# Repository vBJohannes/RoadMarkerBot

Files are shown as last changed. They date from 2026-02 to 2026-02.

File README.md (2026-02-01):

# DISCLAIMER: THIS REPOSITORY IS STILL IN DEVELOPMENT AND NOT ALL PARTS ARE DOCUMENTED YET.

# RoadMarkerBot

A road marking rover with

- skid steering,
- differential GPS (Base + Rover),
- ArduPilot,
- multiple colors,
- dual use as a survey tool.

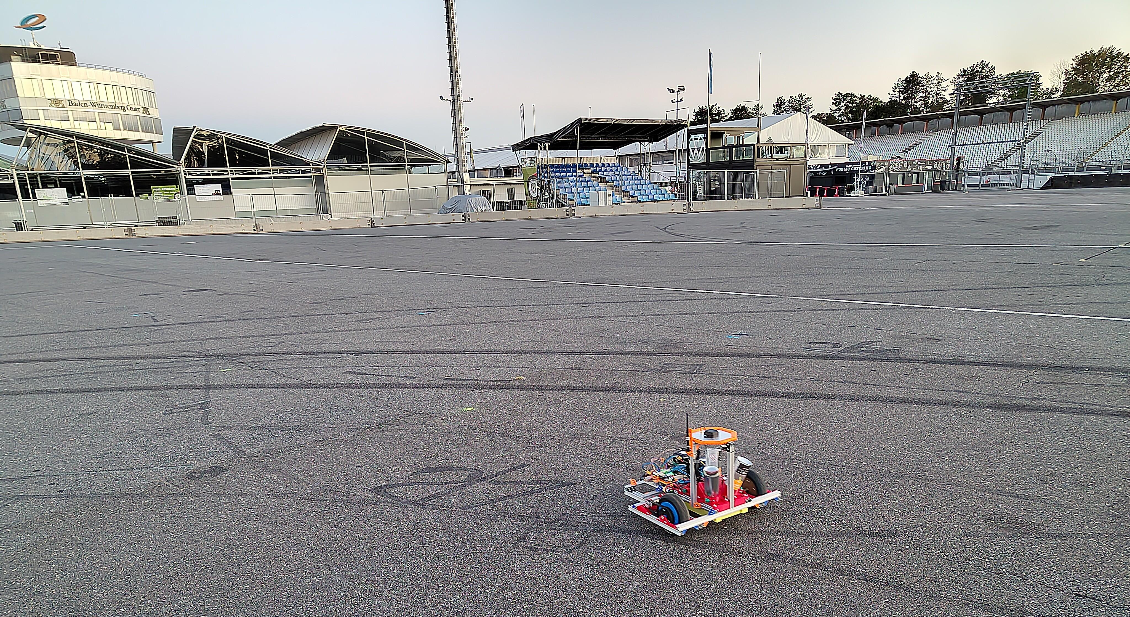
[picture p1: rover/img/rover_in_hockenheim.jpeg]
Bot_during_work


## License

Everything described here can be freely worked in compliance with CC BY-NC-SA 4.0. Please see [License](./LICENSE) for further clarification or check [here](https://creativecommons.org/licenses/by-nc-sa/4.0/deed.en).

## Requirements

- The rover should be able to spray a dot onto pavement at a position defined by GPS.
- The rover should be remotely controllable in order to halt its operation, move around obstacles, and manually drive it for small distances.
- The rover should accept a series of GPS positions in order to mark more complicated tracks.
- The rover should ideally be constructed from off-the-shelf components for easy replacement.
- Rover GPS can be also used as survey tool for manual measurements without the need to move the rover there.

## Solution

The system is divided into subsystems in order to fulfil the requirements.

- The rover is constructed a skid steer robot to realize turning on the spot.
- The rover uses differential GPS for accurate positioning.
- The rover uses ArduPilot in order to provide a platform for vehicle movement and an interface to input target GPS positions.
- The rover can carry four different spray cans at once to use different colors without manual interaction.
- The rover is controlled with an ELRS rc controller in order to provide easy manual input.
- The rover is mainly constucted from aluminium extrusions, 3D prints, rc hobby electronics and available software.

### Architecture

```mermaid
graph TD
    %% Rover
    subgraph ROVER [Rover]
        AP_ROVER(ArduPilot)
        TELEM_ROVER(Rover Communication Module)
        GPS_ROVER(GPS Module)
        GPS_CORR_ROVER(GPS Communication Module)
    end

    subgraph sg1 [GPS Base Station]
        GPS_BASE(GPS Module)
        GPS_CORR_BASE(GPS Communication Module)
    end

    subgraph MP_BASE [Rover Control Base Station]
        AP_BASE(ArduPilot Mission Planner)
        TELEM_BASE(ArduPilot Base Station Communication Module)
    end

    %% Connections
    TELEM_ROVER <-. "Telemetry Data" .-> TELEM_BASE
    GPS_CORR_BASE -. "GPS Correction Data" .-> GPS_CORR_ROVER
    GPS_CORR_ROVER --> GPS_ROVER
    GPS_ROVER --> AP_ROVER
    TELEM_ROVER <--> AP_ROVER
    TELEM_BASE <--> AP_BASE
    GPS_BASE --> GPS_CORR_BASE
```

### In Detail

[Rover Documentation](./rover/README.md)<br>
[GPS Base Station Documentation](./rover/config.md)<br>
[Control Base Station Documentation](./rover/config.md)<br>
[Survey Tool Documentation](./rover/config.md)

## Known Issues

- ArduPilot on Rover currently can only handle around 100 waypoints.
- Rover initialization is currently driving in a large circle to be able to fully use the gyroscope. Magnetometer is currently disabled due to inreliable operation. Hence initial heading is unclear to ArduPilot and it needs to calibrate itself using gyroscope in GPS before starting any mission.
- Starting any movement looks a little jenky and stopping is quite abrupt, which hints to improper PID calibration or ESC configuration.

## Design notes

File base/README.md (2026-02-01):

# GPS Base Station

## Architecture

```mermaid
graph TD
    %% Power Source
    PB(USB Power Bank or<br>other power source) -- "5V via USB" --> BASE_GPS(RTK GPS Module)

    %% Internal Connection
    BASE_GPS -- "UART (RTCM3x)" --> RADIO(Radio Module<br>of Base Station)
    ANT(GPS Antenna) -- "Signal" --> BASE_GPS

    %% Wireless Output
    RADIO -. "868 MHz RTCM Corrections" .-> ROVER(Radio Module<br>on Rover)
```

## Design

The GPS base station is a rather simple setup and was put together from remaining parts and simple 3D printed parts in order to make a solid yet reliable device.
It is about 1000mm in height (to get the antenna off the ground without being too susceptable to wind) and the metal shield at the top has an excessive 300mm diameter (to reduce reflections as much as possible).
It is also built from 20x20mm aluminium extrusions.
The whole system is powered by a regular powerbank and will run for quite some time on it as is only draws about 150mA of current when sending correction data.
The antenna is put to the corner of the upper shield to be also elevated off the ground.

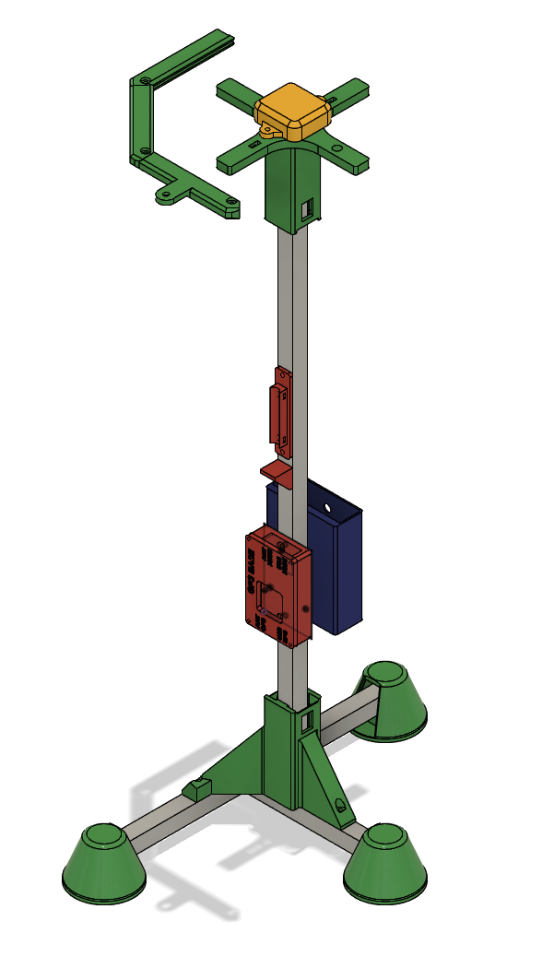
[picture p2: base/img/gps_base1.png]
gps_base1

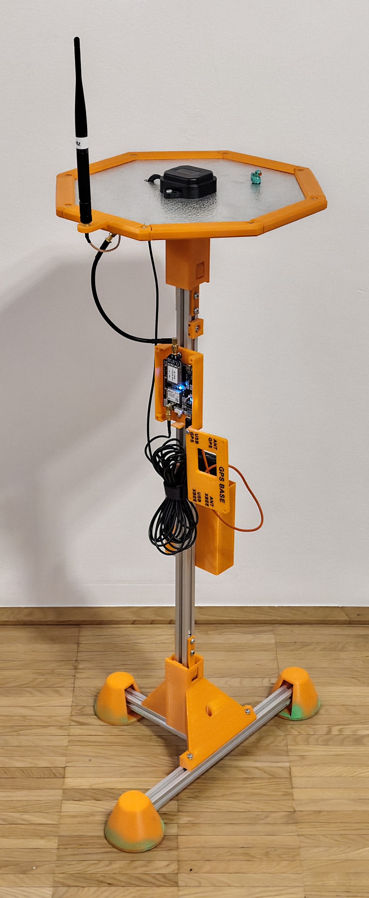
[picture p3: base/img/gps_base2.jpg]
gps_base2

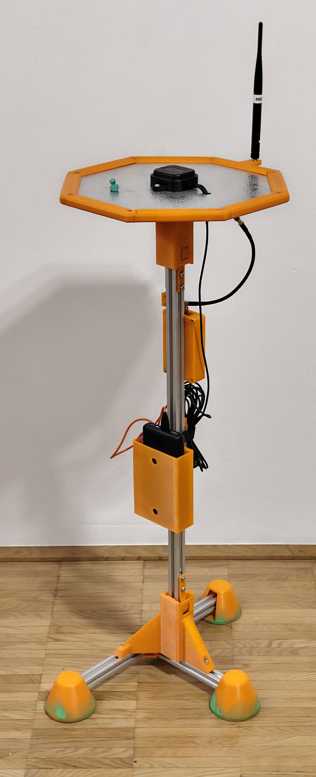
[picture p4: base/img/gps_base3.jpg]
gps_base3

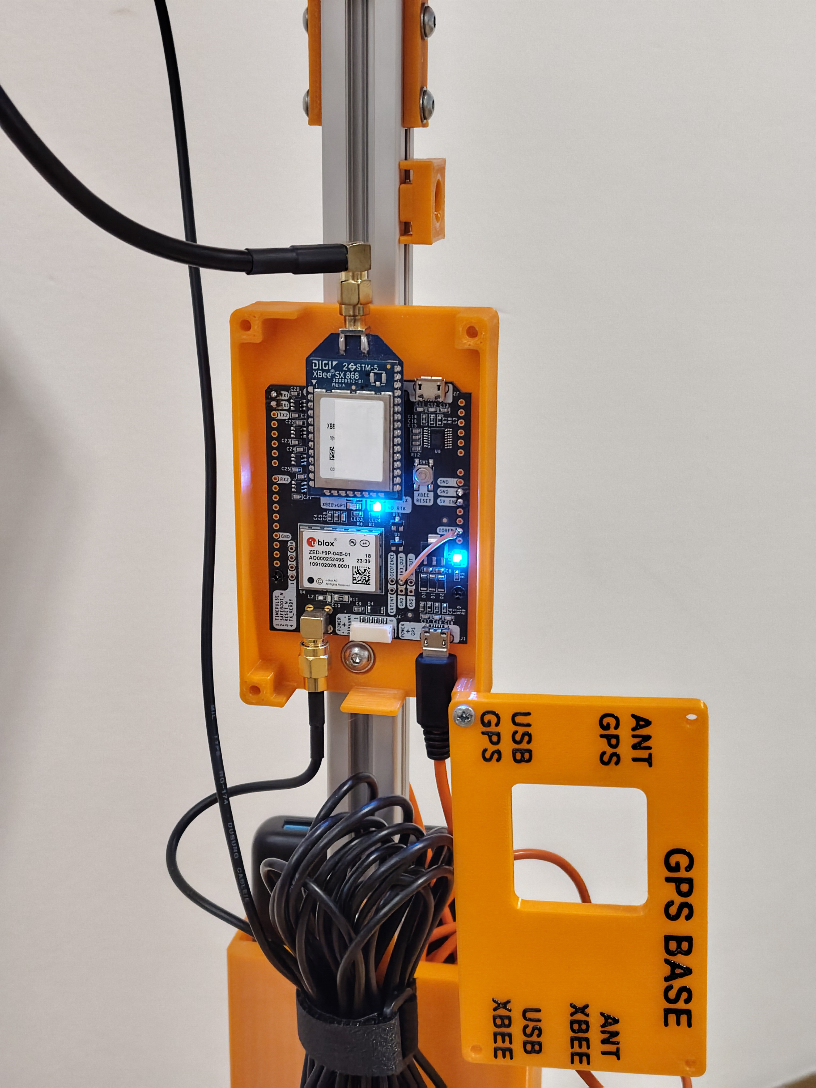
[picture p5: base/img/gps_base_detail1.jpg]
gps_base_detail1

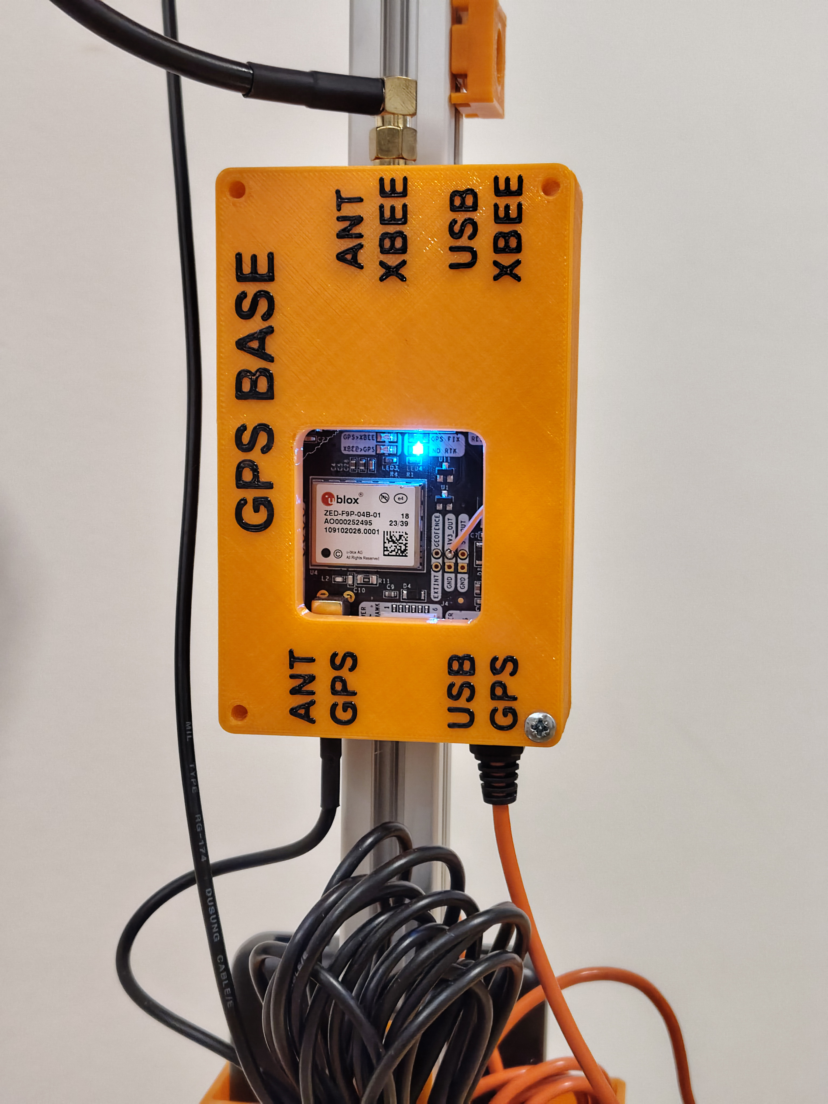
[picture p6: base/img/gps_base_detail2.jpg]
gps_base_detail2


## Usage

- The antenna is placed on a dedicated spot and the ground is marked so the antenna can be placed there repeatedly in the exact same position.
- Ideally the spot is surveyed in by using the antenna, a laptop with [u-Center](https://www.u-blox.com/en/product/u-center), some free Ntrip data service like [RTK2Go](http://rtk2go.com), and the rover GPS config (see [Rover GPS Config](ROVER_LINKS)) to find the exact position the GPS is currently in.
This can then be entered in the config of the GPS base station to run it in fixed mode.
- Both communication modules need to use the same config to communicate properly.

## Links

[GPS Base uBlox Config](./config/uBlox_F9P_Base_config.txt)<br>
[XBee RTCM Config](./config/GPS_RTCM_XBeeSX686_fwA00A.xpro)<br>
[CAD files](./cad/)

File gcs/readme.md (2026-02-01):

# Overview

The Ground Control Station is needed to send the mission waypoints to the rover and communicate with it in the field.
For that it is easiest to run a software like [Mission Planner](https://ardupilot.org/planner/docs/mission-planner-installation.html) and have a reliable connection to the rover.
This can be a USB cable, WiFi, an pair of 868MHz radio modules, or another sort of communication.
In this project a XBee SX 686 module was used, which had the advantage of substantial range at the expense of insanely slow bulk data transfer.
The profile of the modules can be found [HERE](./config/HostTelemetry_XBeeSX686_fwA00A.xpro) and can be used with the [XCTU Tool](https://www.digi.com/products/embedded-systems/digi-xbee/digi-xbee-tools/xctu) to configure the module.
**Hint:** The guard time in that profile is set to 5000ms and this needs to be configured in the XCTU Tool itself as well.

## Mission Planner

For this project v1.3.82 was used.
Choose the proper COM port to get access to the data coming from the XBee module.
In this project a 115200 8N1 was chosen as baud rate.
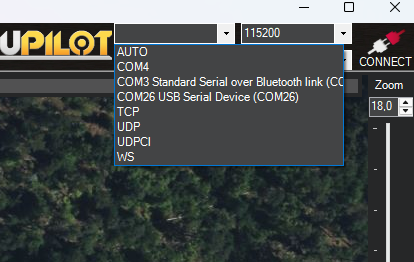
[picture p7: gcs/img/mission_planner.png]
mission_planner


## Equipment

### Case

In this project a nice little case was designed, that was intended to house two modules, but was used by only one in the end.
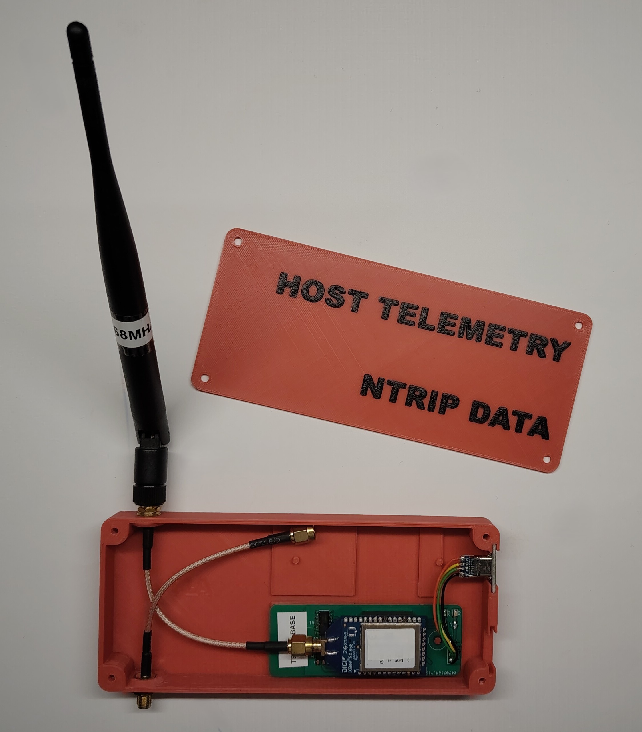
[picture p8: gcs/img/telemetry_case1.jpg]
telemetry_case1

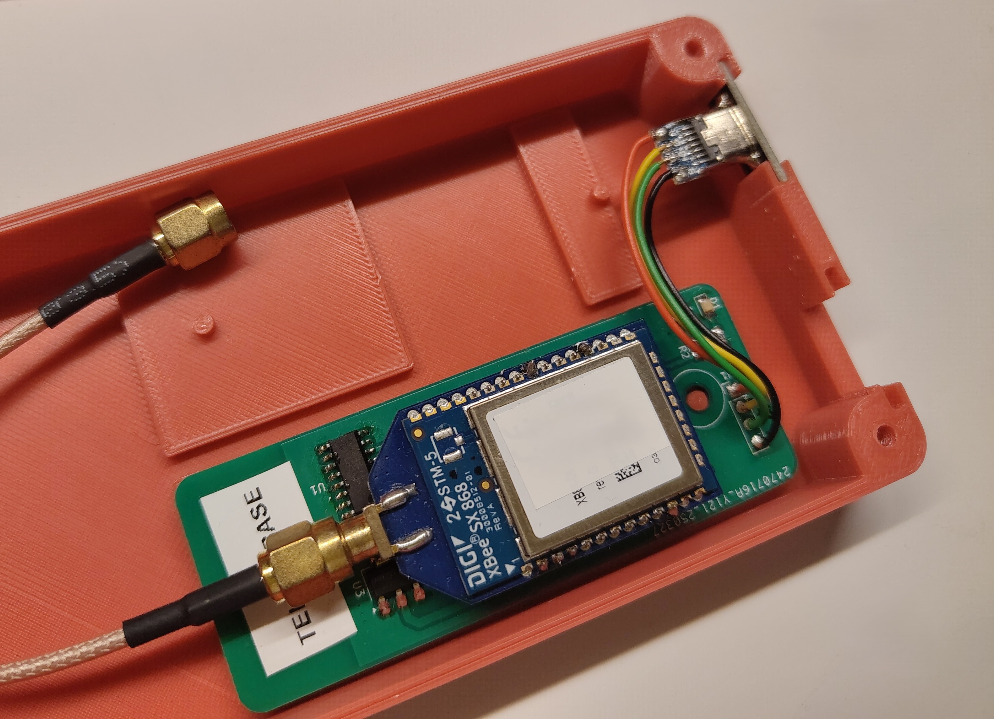
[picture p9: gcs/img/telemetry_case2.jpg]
telemetry_case2


### PCB

For this project a custom PCB was designed. The KiCAD project can be found [HERE](./cad/telemetry_pcb.zip).
The lower picture shows an earlier version of the board.
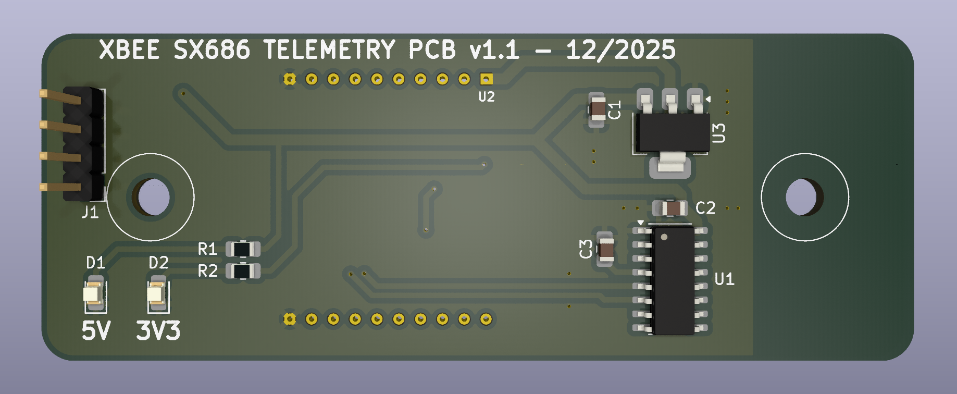
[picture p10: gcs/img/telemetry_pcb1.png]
telemetry_pcb1

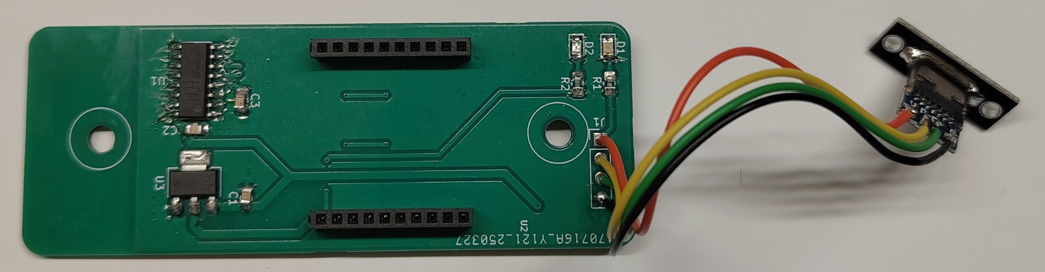
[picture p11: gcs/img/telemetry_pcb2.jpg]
telemetry_pcb2


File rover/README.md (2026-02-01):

# Rover

## Logical Architecture

```mermaid
graph TD
    %% Central Unit
    subgraph PIXHAWK [Pixhawk 2.4.8]
        AP(ArduPilot)
        CPU(Processor)
        IMU_INT(Internal Gyro / IMU)
    end

    %% Sensors & Inputs
    IMU_EXT(External Gyro) -- "I2C Bus" --> PIXHAWK
    GPS_ROVER(RTK GPS Rover) -- "UART" --> PIXHAWK
    RC_REC(RC Receiver) -- "UART" --> PIXHAWK
    TELE(Telemetry Module) -- "UART (MAVLink)" --> PIXHAWK
    
    %% Power Monitoring (New)
    PWR_SENS(Power Sensor) -- "Analog (U/I Data)" --> PIXHAWK

    %% Wireless Links
    GCS(Ground Control Station<br>Ardupilot Mission Planner) <-. "868 MHz Radio" .-> TELE
    Remote(Remote Control<br>with EdgeTX) <-. "ELRS Link" .-> RC_REC

    %% GPS RTK
    GPS_BASE(RTK GPS Base Station) -. "868 MHz RTCM Corrections" .-> GPS_ROVER

    %% Actuators (Outputs)
    PIXHAWK -- "PWM" --> ESC(ESC Motor Controller<br>AM32)
    ESC --> MOT(2x BLDC Drive Motors)
    
    PIXHAWK -- "PWM" --> SER(4x Servos<br>for Spray Cans)
```

## Electrical Archtecture

```mermaid
graph TD
    %% Power Source and Monitoring
    BAT(4-6S LiPo Battery) --> SENS(Power Sensor / <br/>Current & Voltage)
    
    %% Monitoring Link
    SENS -- "Analog Data (U/I)" --> PH(Pixhawk Flight Controller)

    %% Direct Power Distribution
    SENS --> ESC(Dual ESC<br/>Motor Controller)
    SENS --> REG1(5V Voltage Regulator<br/>Logic Supply)
    SENS --> REG2(5V Voltage Regulator<br/>Servo Supply)

    %% Drive System
    ESC --> M1(Drive Motor Left)
    ESC --> M2(Drive Motor Right)

    %% Logic Supply Path
    REG1 --> PH
    PH --> GPS(RTK GPS Rover)
    PH --> TELE(Telemetry Module)
    PH --> RC(RC Receiver)
    PH --> GYRO(External Gyro / IMU)

    %% Servo Supply Path
    REG2 --> SERVO_BUS(Servo Rail)
    SERVO_BUS --> S_ALL(4x Servos)

    %% Control Signals (Simplified)
    PH -. "PWM" .-> ESC
    PH -. "PWM" .-> S_ALL
```

## Design

The robot was designed as a skid steer vehicle with a trailing third wheel.
An extensible design was chosen to allow quick modifications.
Overall vehicle dimensions: width 600 mm, length 500 mm, height 400 mm

Built with:

- 20×20 mm aluminium extrusions to mount various components
- high gear reduction on the motors for precise maneuvers
- simple power supply using 18 V batteries compatible with Makita or Bosch
- readily available hobby-model parts
- autonomous control via ArduPilot software
- four spray cans can be mounted and all spray to the same point

### Frame

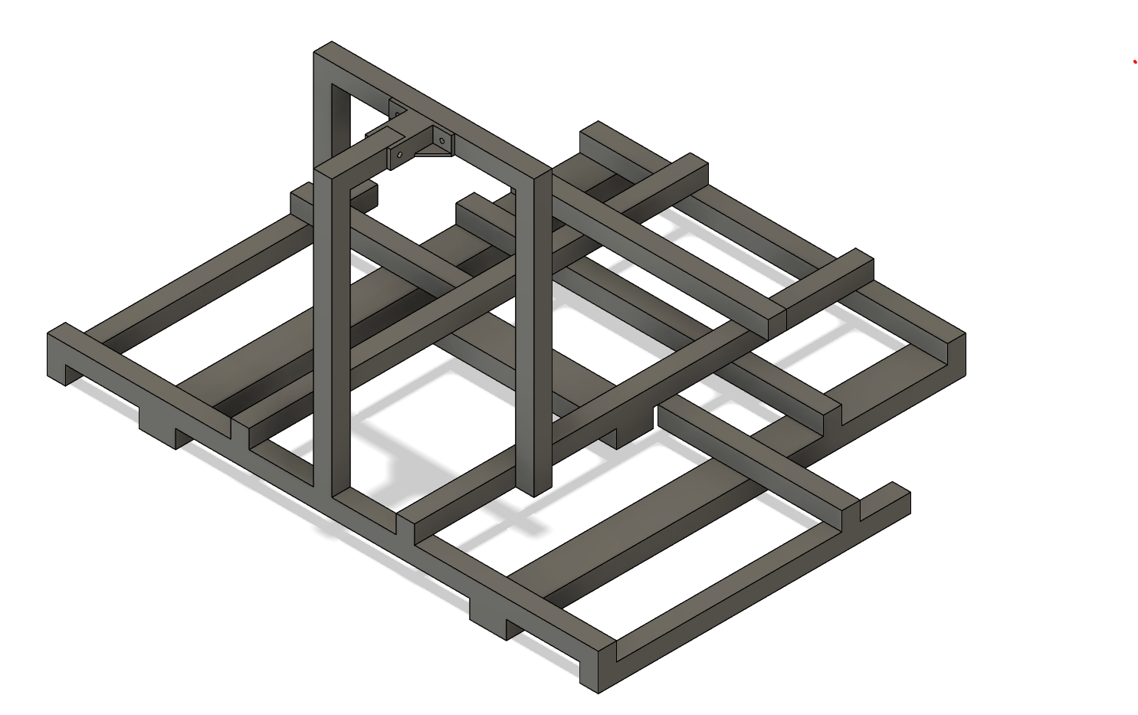
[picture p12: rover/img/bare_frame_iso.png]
frame_iso

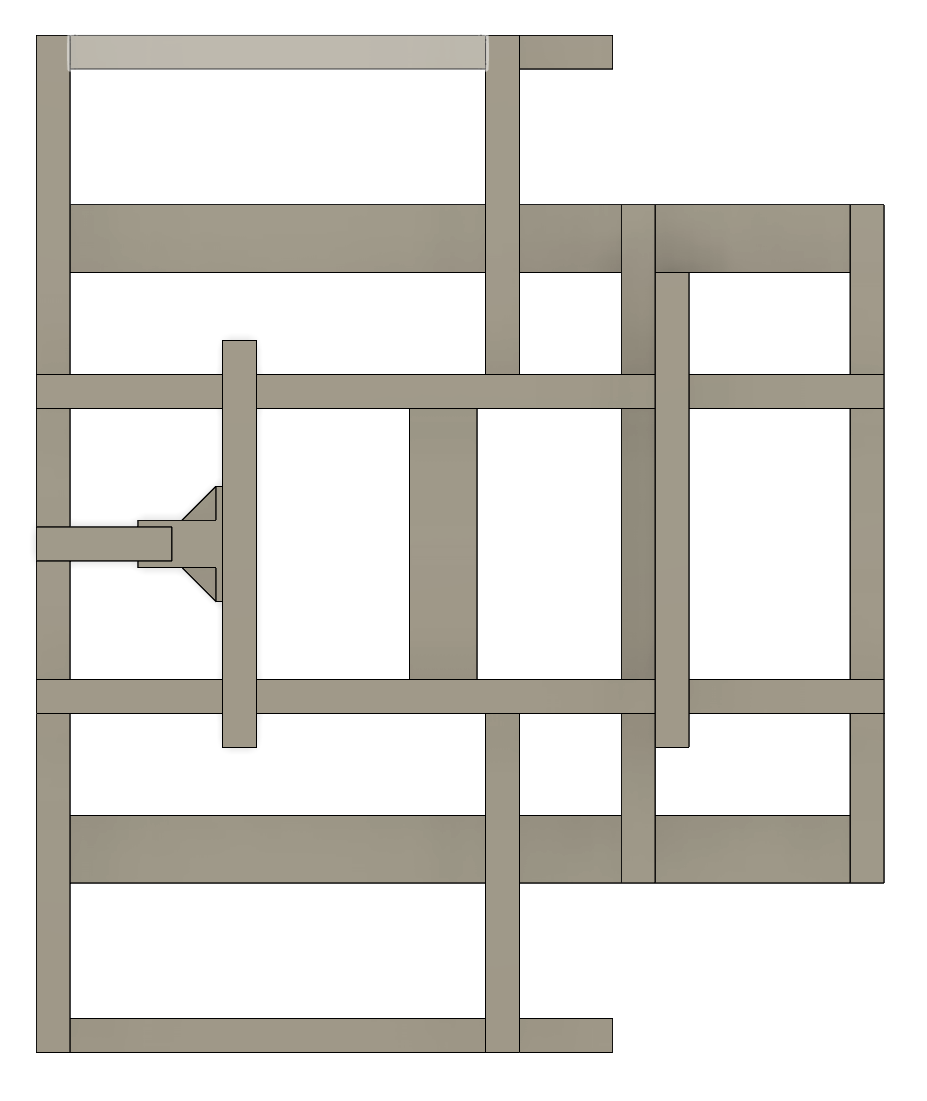
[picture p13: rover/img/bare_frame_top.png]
frame_top


### Wheel Assembly

For this project powerful and low-KV motors were used.
The purpose was to make small corrections with the high torque and low rpm.
In addition a reduction of about 45:1 was achieved by a gearbox (19:1) and pulleys (2.35:1).
This specific BLDC motor is a *Robbe 5052 410K/V* rated for 50A at 6S.
Due to the reduction the rover reaches speeds of about 5km/h.
The wheel itself is a solid rubber 190mm replacement wheel for e-scooters and was adapted to carry a pully.
The third wheel in the back was purchased in a local hardware store and the wheel itself was reprinted in TPU in order to run smoother on hard surfaces like concrete.
All the parts can be found in [this archive (MISSING)](./cad/motor_wheel_parts.zip).

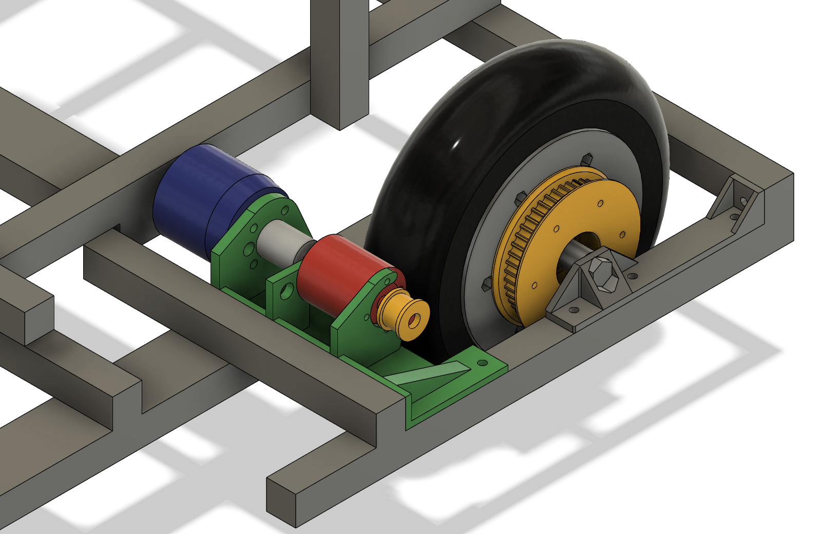
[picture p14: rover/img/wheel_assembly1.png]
wheel_assembly1

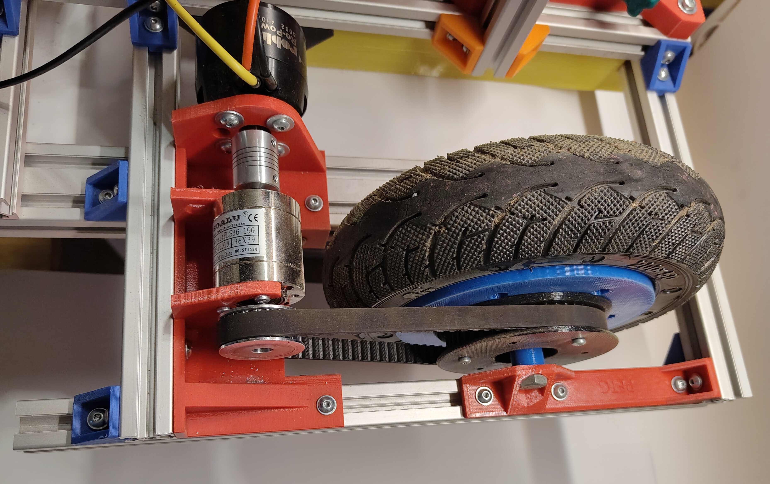
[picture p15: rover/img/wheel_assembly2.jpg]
wheel_assembly2

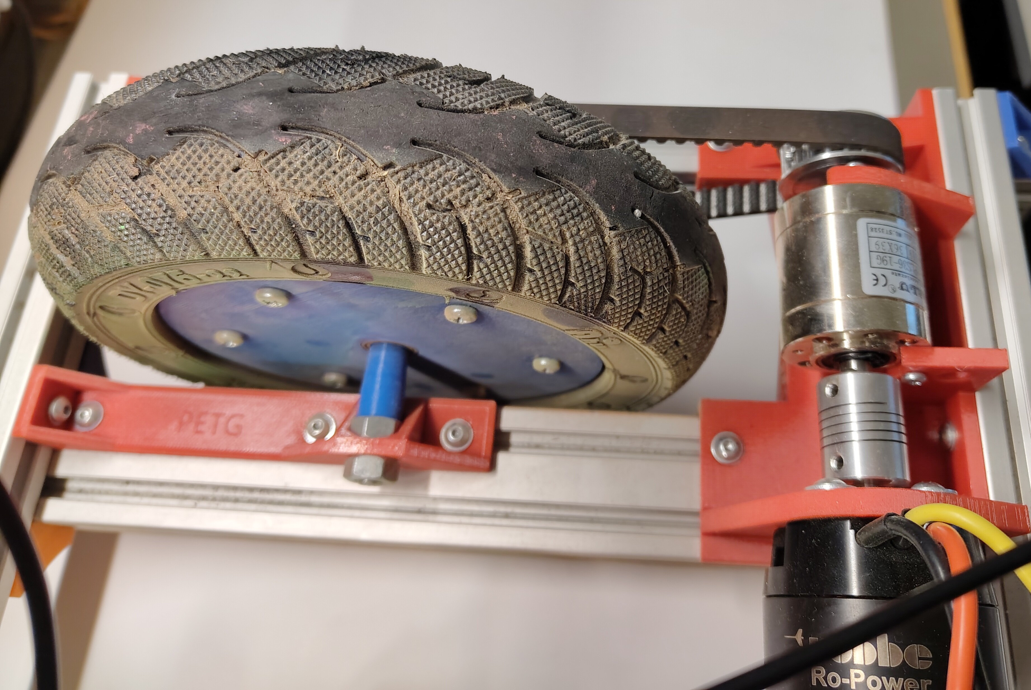
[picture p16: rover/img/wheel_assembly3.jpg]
wheel_assembly3

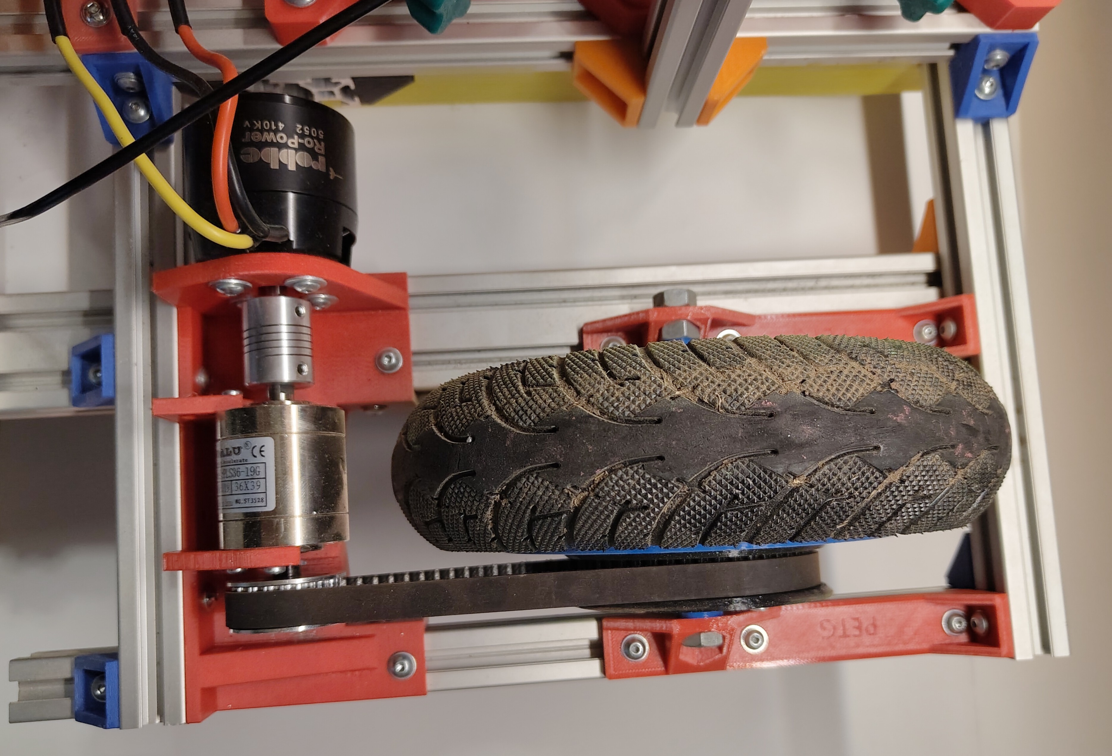
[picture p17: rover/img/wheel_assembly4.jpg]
wheel_assembly4

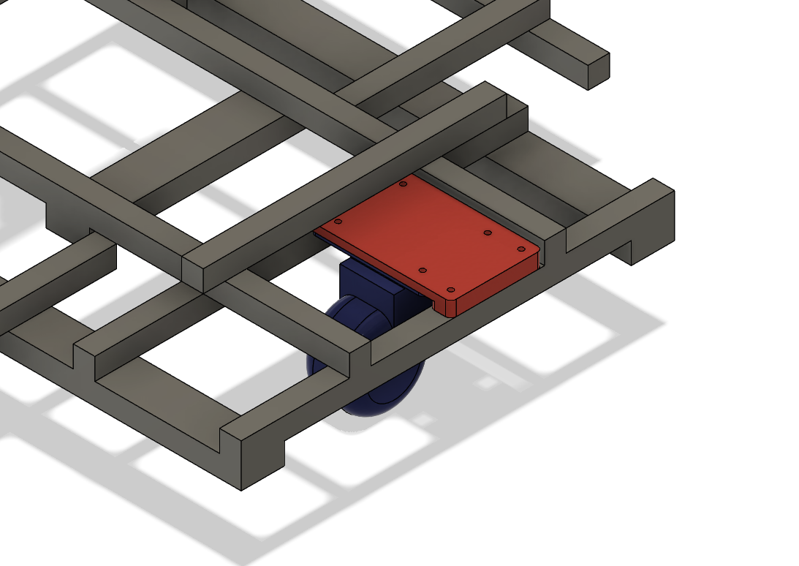
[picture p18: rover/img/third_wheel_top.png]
third_wheel_top

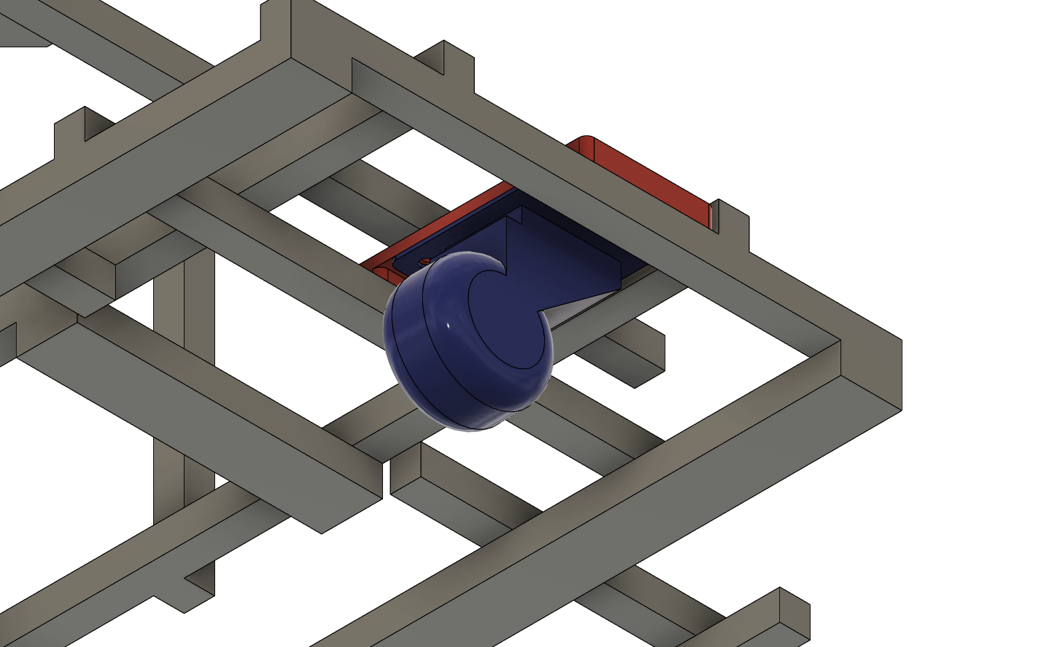
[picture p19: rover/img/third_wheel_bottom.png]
third_wheel_bottom

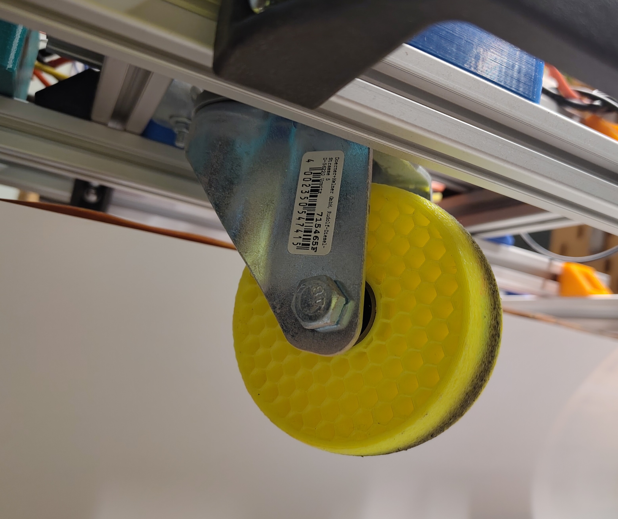
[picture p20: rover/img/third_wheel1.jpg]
third_wheel1

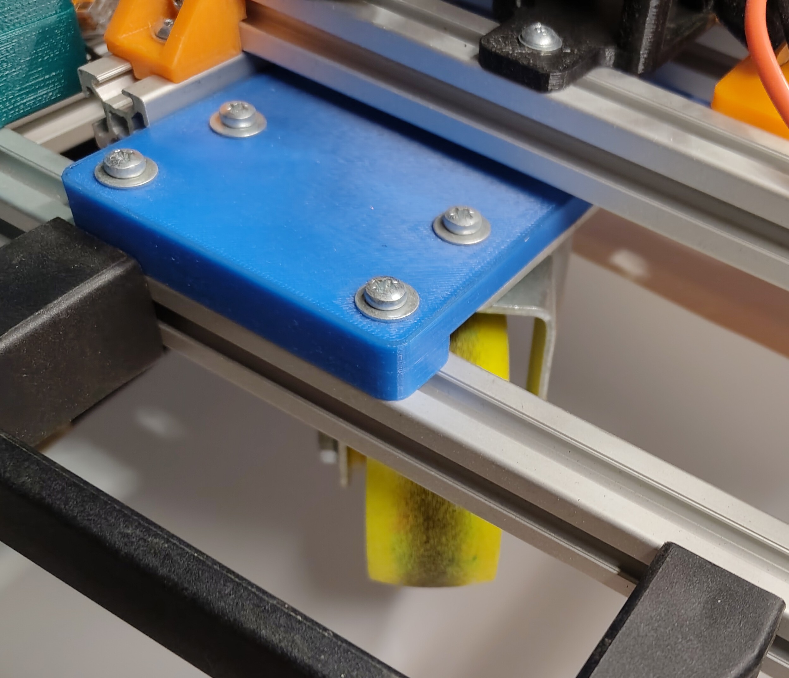
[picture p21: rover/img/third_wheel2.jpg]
third_wheel2


### GPS

On the rover and the base station a board with *uBlox F9P* module is used.
The particular part is an *ArduSimple simpleRTK2B* with *Radio Module Long Range (LR)* and *ANN-MB-00* antenna.
The GPS module is mounted below the connection PCB.
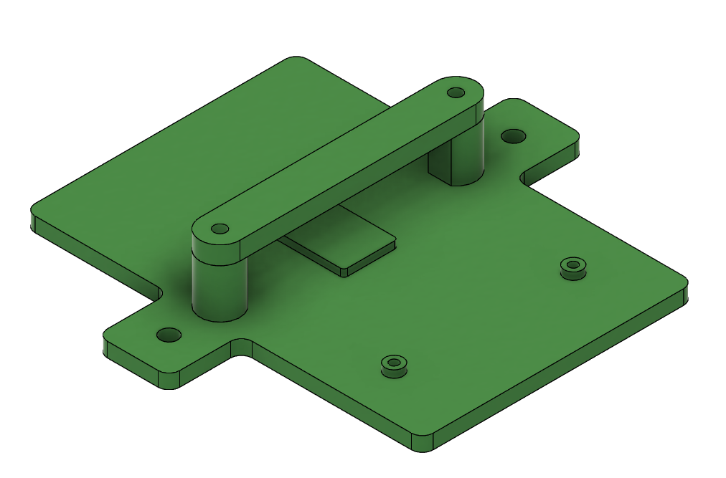
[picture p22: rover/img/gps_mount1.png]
gps_mount1

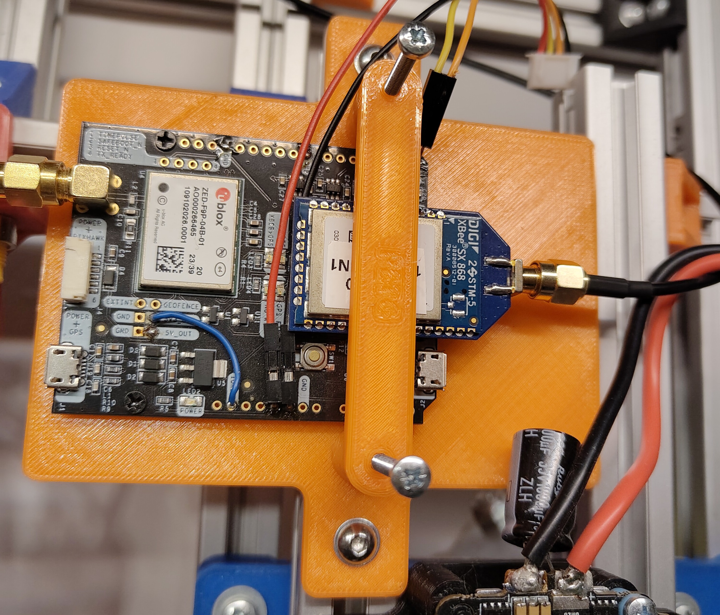
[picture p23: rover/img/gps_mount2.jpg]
gps_mount2

The step files for the base can be found [HERE](./cad/gps_mount_base.step) and the one for the retainer can be found [HERE](./cad/gps_mount_retainer.step).
The config file for the GPS can be found [HERE](./config/uBlox_F9P_Rover_config.txt) and can be applied using the [u-Center](https://www.u-blox.com/en/product/u-center).
The config file for the radio module can be found [HERE](../base/config/GPS_RTCM_XBeeSX686_fwA00A.xpro) and should also be used on the [Base Station](base_station_gps).
The antenna is placed on a 200x200x2mm sheet of aluminium to filter out ground reflections.

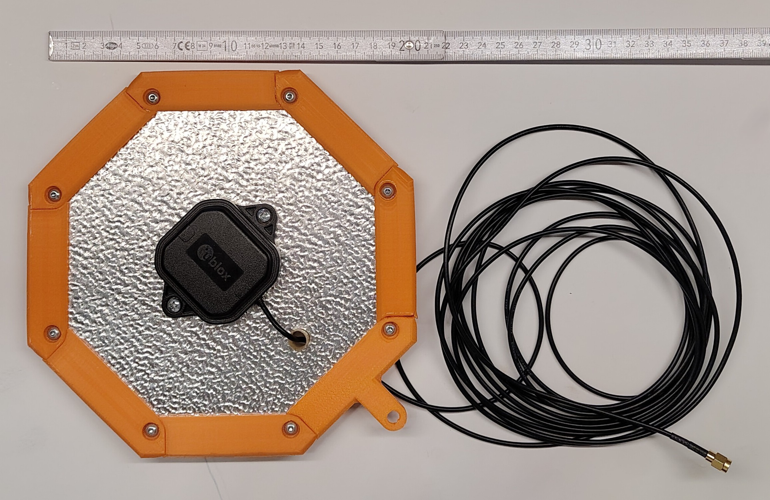
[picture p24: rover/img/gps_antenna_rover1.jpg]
gps_antenna_rover1


### Spray Can Pods

The spray can pod is designed in a way, that all four cans mark the same spot right in the center of the (imaginary) front axle.
The pod is printed in one piece and is intended to make the frame more rigid.
The cans can be attached and detached after loosening the thumb screw.
This pod is designed around a chalk marking spray from Technima.
On the under side the trigger of the cans are activated by servos, which are in turn covered to prevent dirt and debris from damaging the rover while in operation.
So the whole setup consists of a the [four-way bay (MISSING)](./cad/bays.step), [the can clamps (MISSING)](./cad/can_clamp.step), [thumb screws (MISSING)](./cad/thumb_screws.step) and the [bottom cover (MISSING)](./cad/bottom_cover.step).

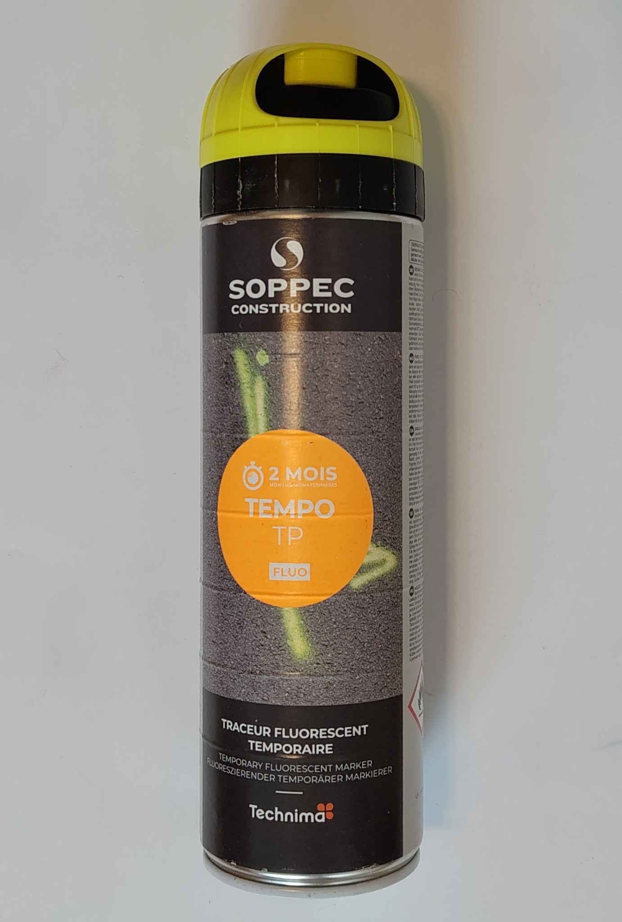
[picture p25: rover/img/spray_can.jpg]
spray_can

pod1
pod2
pod3

### Power Supply

For this project the focus was availibility of power sources, so an adapter to run off batteries compatible with Bosch's 18V system.
Initially two batteries were planned, but due to very small power draw, the rover runs for several kilometers on a single battery.
Due to reverse current protection a battery can be added during operation and the other one can be pull from the rover without interrupting operation.
The parts to reprint this part can be found [in this archive (MISSING)](./cad/battery_port.zip).

battery_port1

### Flight Controller

As flight controller a *Pixhawk 2.4.8* was used due to high availability at reasonable prices.
This comes at the cost of limited computational power when handling waypoints.
The flight controller has enough IO ports and can run ArduPilot, which was used for the project.
The config file for the flight controller can be found [HERE](pixhawk_config.txt).
In order to fix the flight controller to the frame two side supports are used.
The step file can be found [HERE](./pixhawk_mount.step).
It has a cutout for the USB port and as it is symmetric, it is needed twice.

pixhawk_mount1
pixhawk_mount2

### ESC Parts

For this project a BLHELI32 compatible ESC was used due to its configurability.
The exact part was a *T-Motor P60A v2*, which proides 60A from 3-6S LiPo batteries.
To run the motors, this config was used on output M3 and M4.
For configuration a *Sequre ESC-Link* and the *BlHeli32 Suite* was used.
The ESC itself is mounted to the frame and also provides connectors for the motor wiring.
Both step files can be found [HERE](./esc_mount.step) and [HERE](./banana_plug_mount.step).

esc_mount1
esc_mount2
banana_mount1

### Connection PCB

This board is intended to have a common connector for all sensors and actors connected to the Pixhawk.
This specifically applies to GPS, Servos, ELRS receiver, ESC, and the telemetry radio module.
It is also intended to be used to convert voltage from battery to 5V and 3.3V.
The KiCad file can be found [HERE](dotty2_adapter_board.zip) and the STEP file to hold down the radio module can be found [HERE](dotty2_adpater_board_radio_module_retainer.step).

dotty2_adapter_pcb1
dotty2_adapter_pcb2
dotty2_adapter_board1
dotty2_adapter_board2

## Configuration

### ESC Configuration

Both used motor ports M3, M4 were configured like this.

esc_config

### Pixhawk

As this is the heart of the project a lot of different configurations were used. All of them are combined in the parameter file linked below.
Details are explained in the following sections.

#### UART

The Pixhawk has 6 UARTs, which are used for USB (UART0), ELRS radio module communication (UART1), host telemetry back to MissionPlanner (UART2), and GPS data (UART3).
The last two UARTs are not used.

config_uart

#### Servo Output

The servo output is one of the relevant parts of the rover.
The first four channels belong to the spray pod servos.
They are all linked to two certain RC input channels, which map to a a push button on the RC controller to manually fire all spray pods (at once). This is mainly used for testing or for manually marking spots once the rover moved there.
Special attention needs to be paid to the trim value, which represents the idle state of each servo.
As the servos in the pods are mirrored, the values change from pod to pod.
Ouput channel 9 and 10 are used for the motor controller.
As the motor can also go backwards, 1500 is the idle/standstill value.

config_servo

#### RC Input

As the remote control also sets other options on the pixhawk, a few more RCINx channels are mapped to special functions. The mode the rover is supposed to go in (manual/auto) in order to start or pause executing a mission.

config_rcin5

There is also the arming setting, which is set with another toggle switch on the remote.

config_rcin6

#### Power Measurement

To have an overview over the power consumption and battery voltage a power meter is used. The exact battery capacity varied over the development and is not used for any sort of alarm. The configuration looks like this:

config_power

## Links

[ArduPilot Config File](./config/PixhawkArduPilot.param)

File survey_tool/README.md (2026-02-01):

# Survey Tool

## Architecture

```mermaid
graph TD
    
    %% Communication & Interface
    subgraph Handheld_Unit [Survey Tool]
        ESP
        BTN(Push Button)
        GPS_ROV(GPS from Rover)
        RADIO(Radio Module<br>from Rover)
    end
    ESP(ESP8266)

    %% Data Connections
    RADIO -- "UART (RTCM3x)" --> GPS_ROV
    GPS_ROV -- "UART (NMEA)" --> ESP
    BTN -- "Trigger" --> ESP

    %% External Links
    BASE(RTK Base Station) -. "868 MHz RCTM Corrections" .-> RADIO
    ESP -- "UART (NMEA) via<br>USB or Wifi" --> SERVER(Mobile Device)
```

## Design

full_model

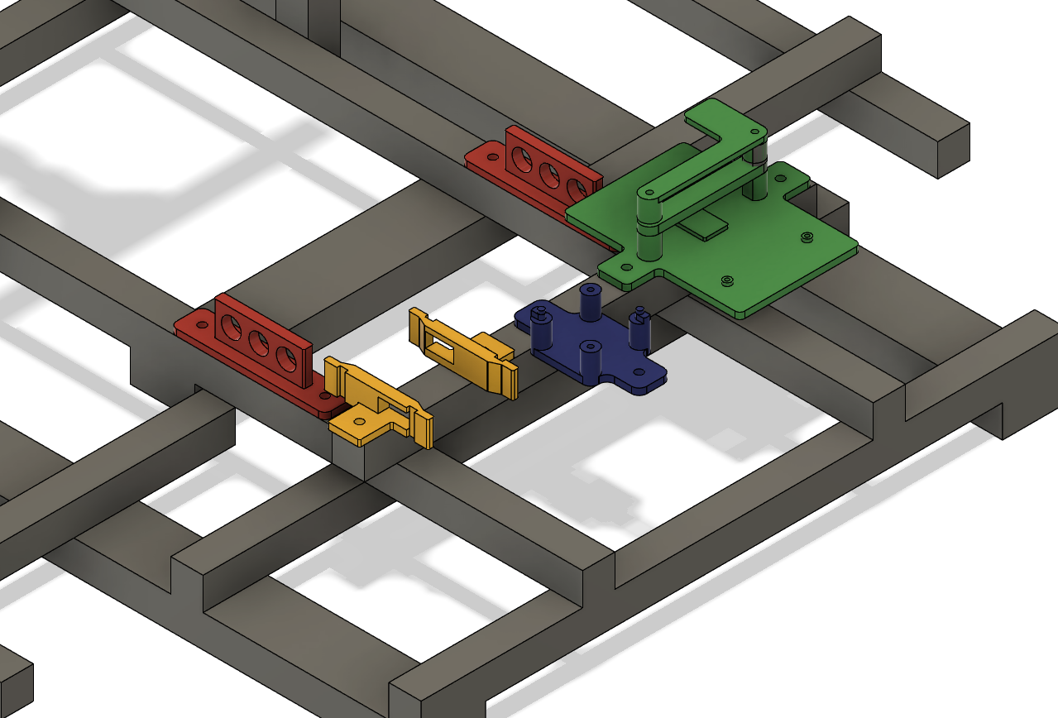
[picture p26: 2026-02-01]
rover/img/mounts_for_electronics.png

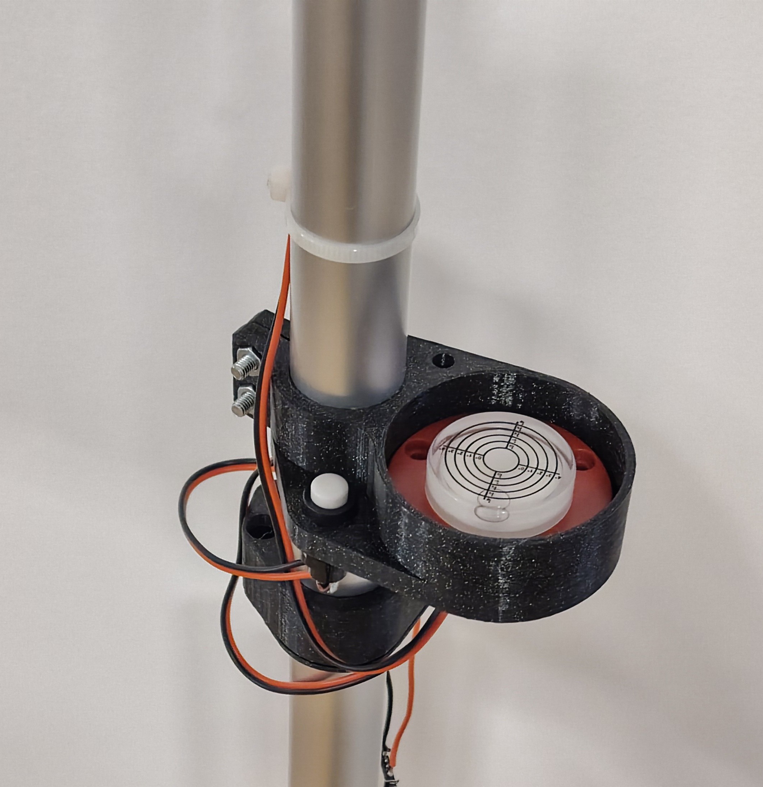
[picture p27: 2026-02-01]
survey_tool/img/survey_tool_detail3.jpg

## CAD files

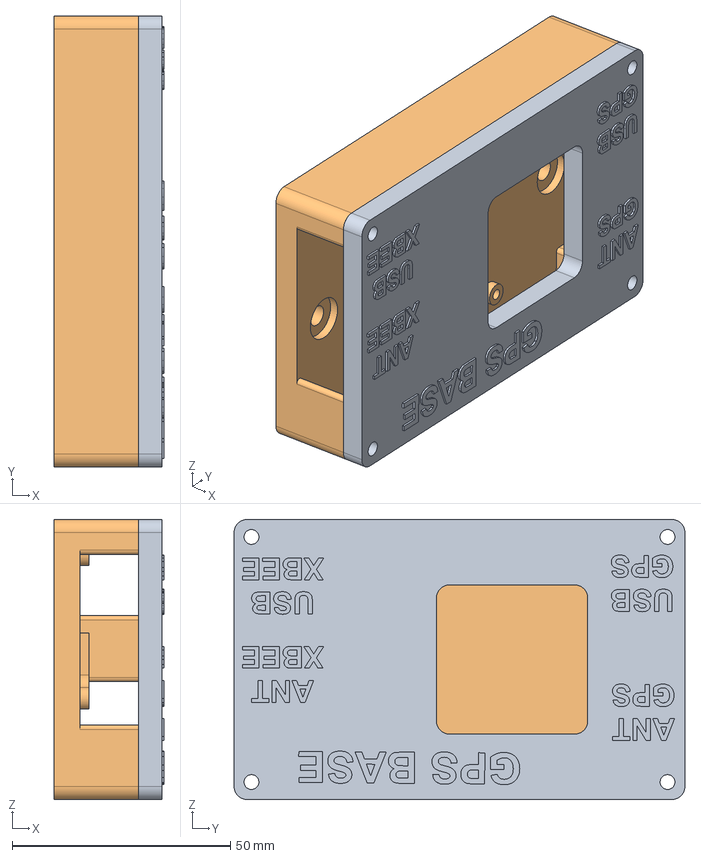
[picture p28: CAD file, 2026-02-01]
base/cad/GpsModuleMount.step
25.2 x 103.4 x 64.2 mm

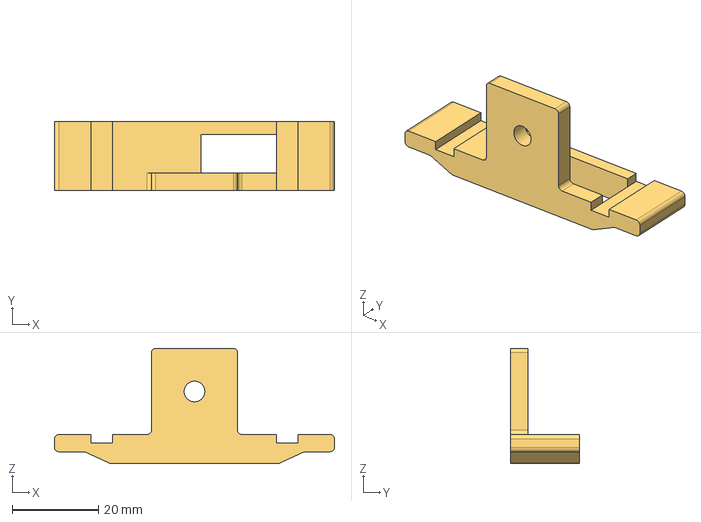
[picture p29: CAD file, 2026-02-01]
rover/cad/pixwhawk_mount.step
65.0 x 16.0 x 26.8 mm

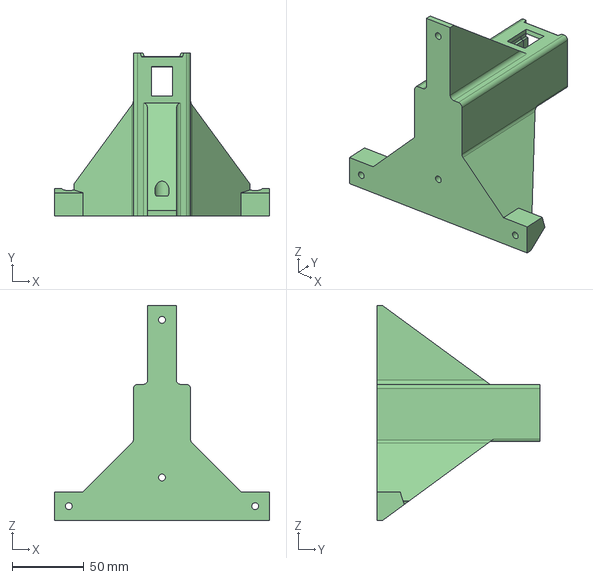
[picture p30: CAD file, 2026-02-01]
base/cad/AntennaMountBottom.step
150.0 x 114.0 x 150.0 mm

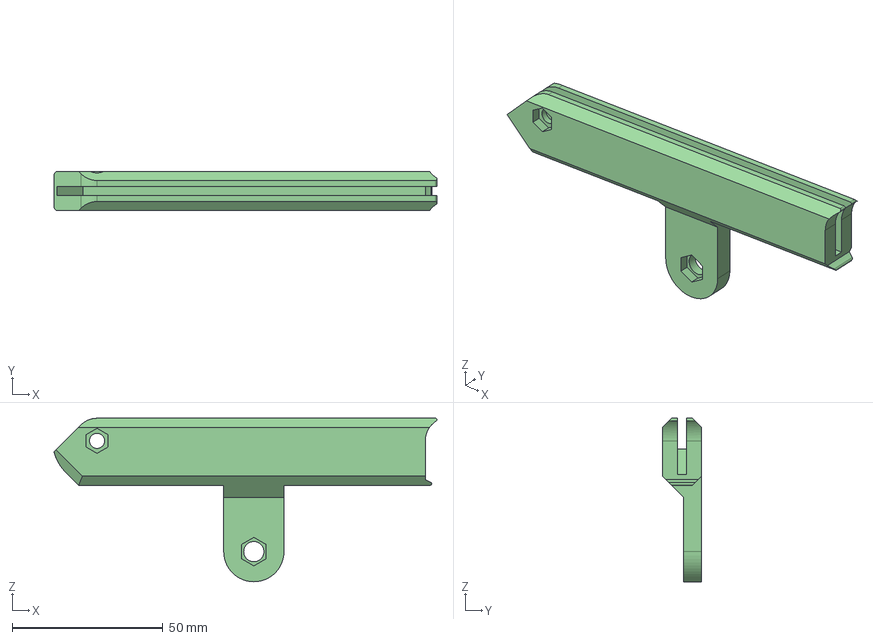
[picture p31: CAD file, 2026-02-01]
base/cad/AntennaDiskBorderWithAntennaMount.step
127.0 x 13.0 x 54.2 mm

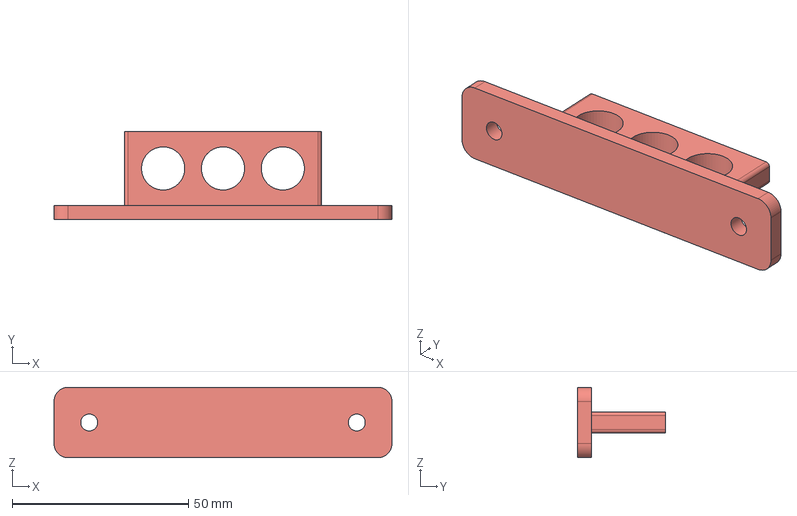
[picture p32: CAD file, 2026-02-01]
rover/cad/banana_plug_mount.step
96.0 x 25.0 x 20.0 mm

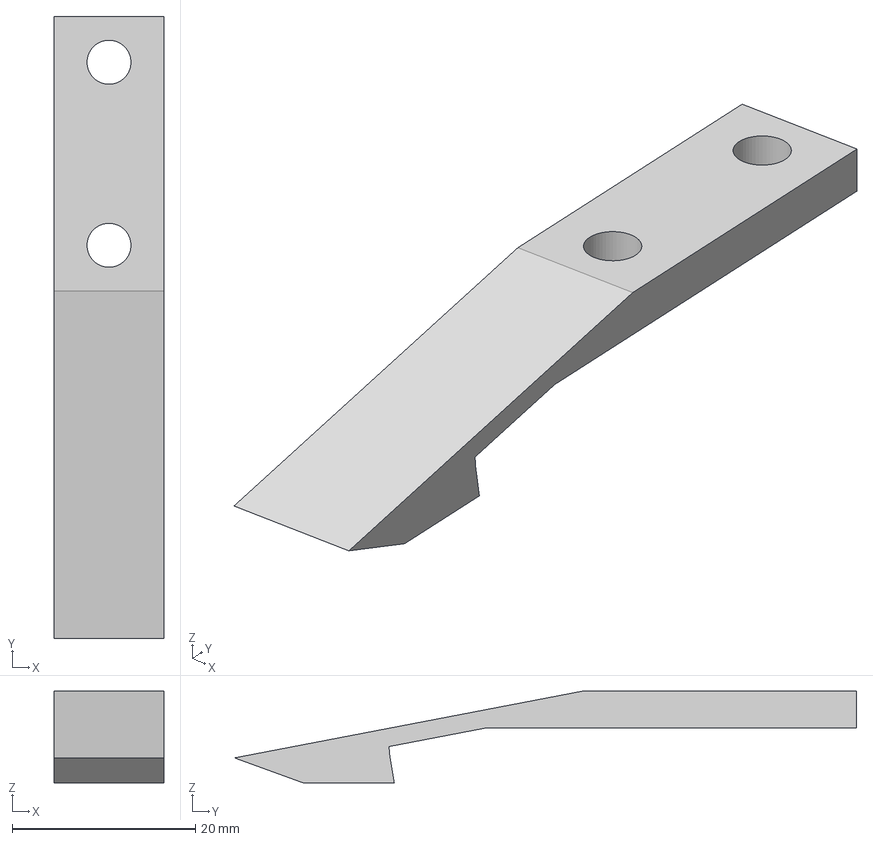
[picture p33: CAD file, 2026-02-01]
base/cad/AntennaMountRetainer.step
12.0 x 68.0 x 10.0 mm

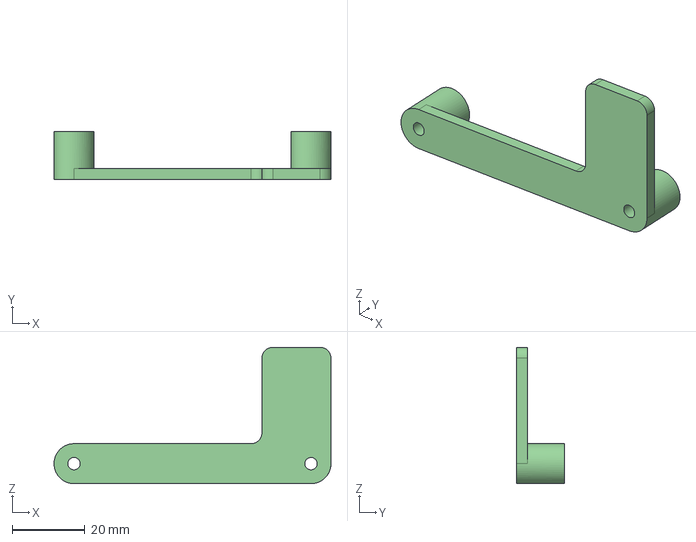
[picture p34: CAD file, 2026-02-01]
rover/cad/dotty2_adpater_board_radio_module_retainer.step
76.2 x 13.1 x 37.5 mm

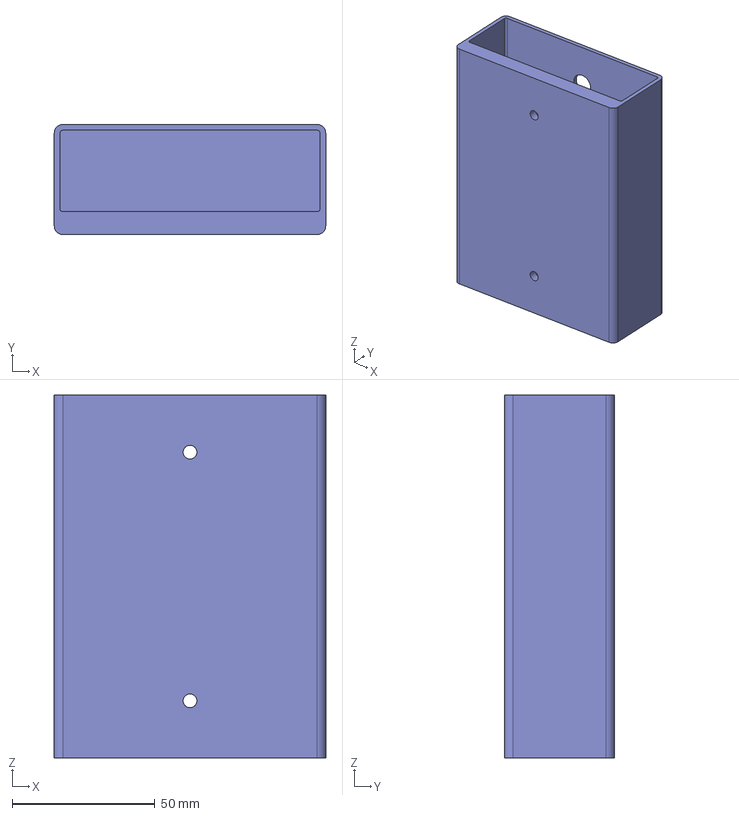
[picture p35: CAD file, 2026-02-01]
base/cad/PowerbankMount.step
95.0 x 38.5 x 127.0 mm

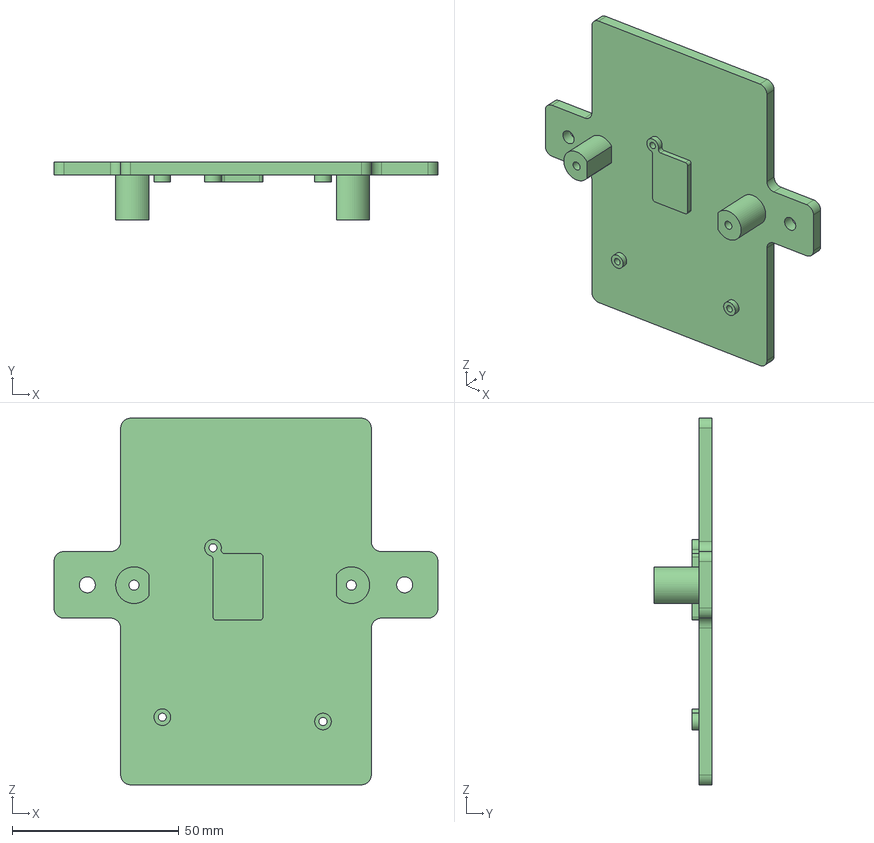
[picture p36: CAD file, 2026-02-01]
rover/cad/gps_mount_base.step
115.2 x 17.5 x 110.0 mm

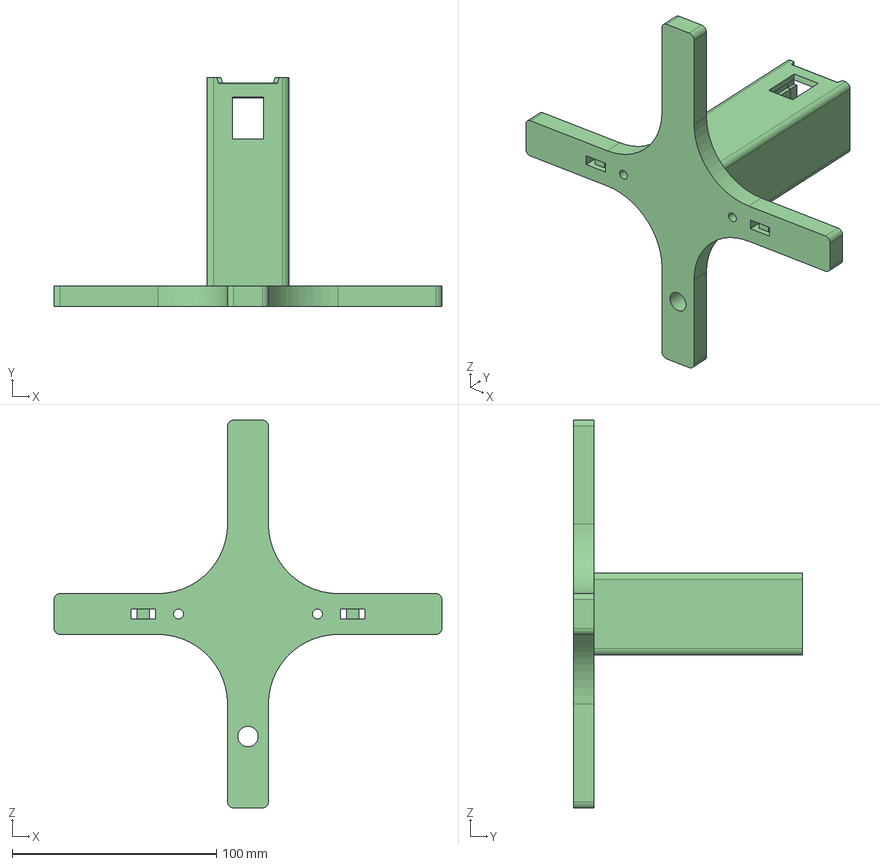
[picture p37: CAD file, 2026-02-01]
base/cad/AntennaMountTop.step
190.0 x 112.0 x 190.0 mm

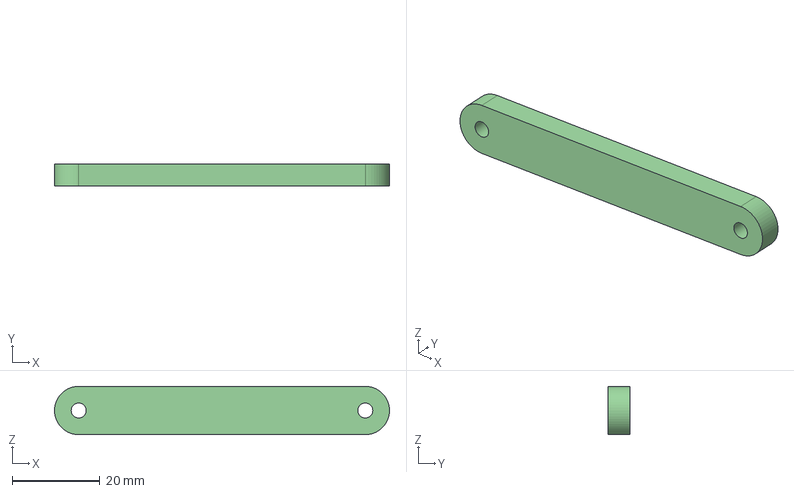
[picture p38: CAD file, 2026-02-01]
rover/cad/gps_mount_retainer.step
76.2 x 5.00 x 11.0 mm

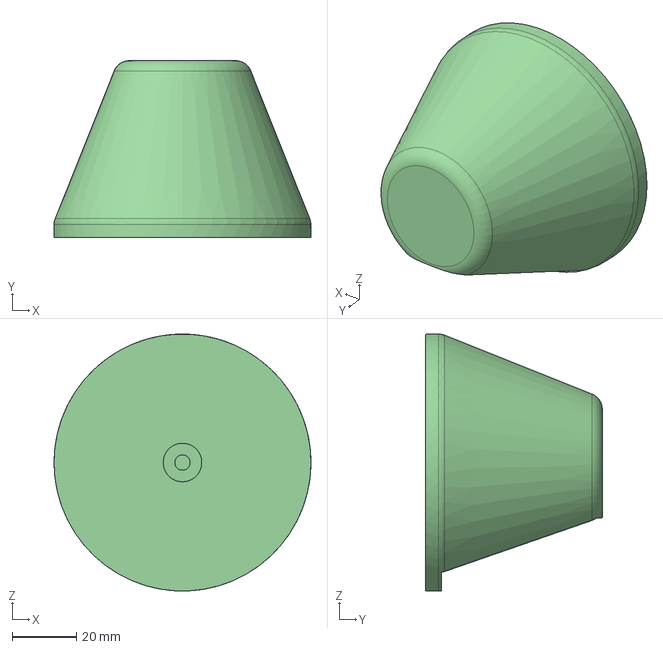
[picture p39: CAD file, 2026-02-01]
base/cad/AntennaFoot.step
80.0 x 55.0 x 80.0 mm

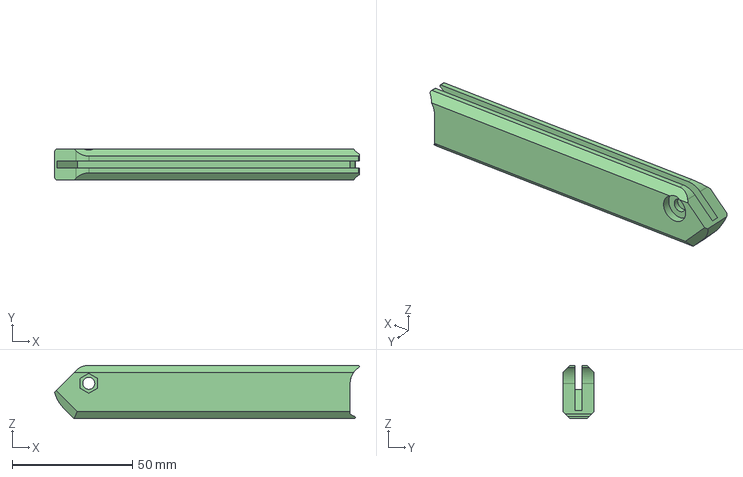
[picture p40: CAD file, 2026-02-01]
base/cad/AntennaDiskBorder.step
127.0 x 13.0 x 22.2 mm

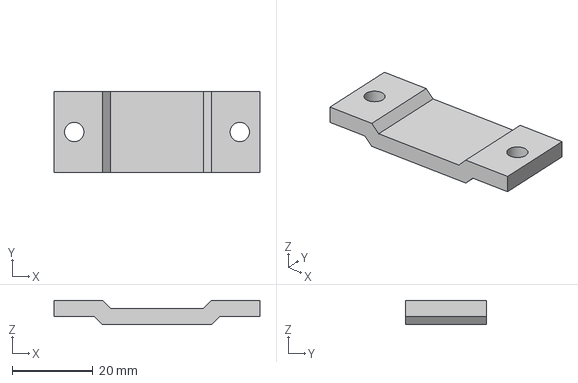
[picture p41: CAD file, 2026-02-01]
base/cad/WireClamp.step
51.0 x 20.0 x 6.00 mm

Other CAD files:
rover/cad/esc_mount.step

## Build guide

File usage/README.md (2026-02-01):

# Usage

## Create Waypoint Mission

## Workflow for Running a Mission

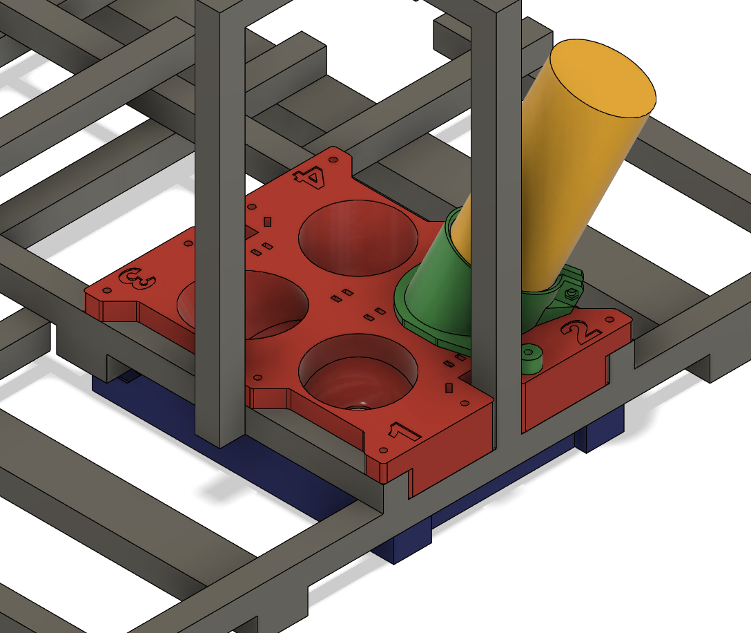
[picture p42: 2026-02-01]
rover/img/sprayer_assembly.png

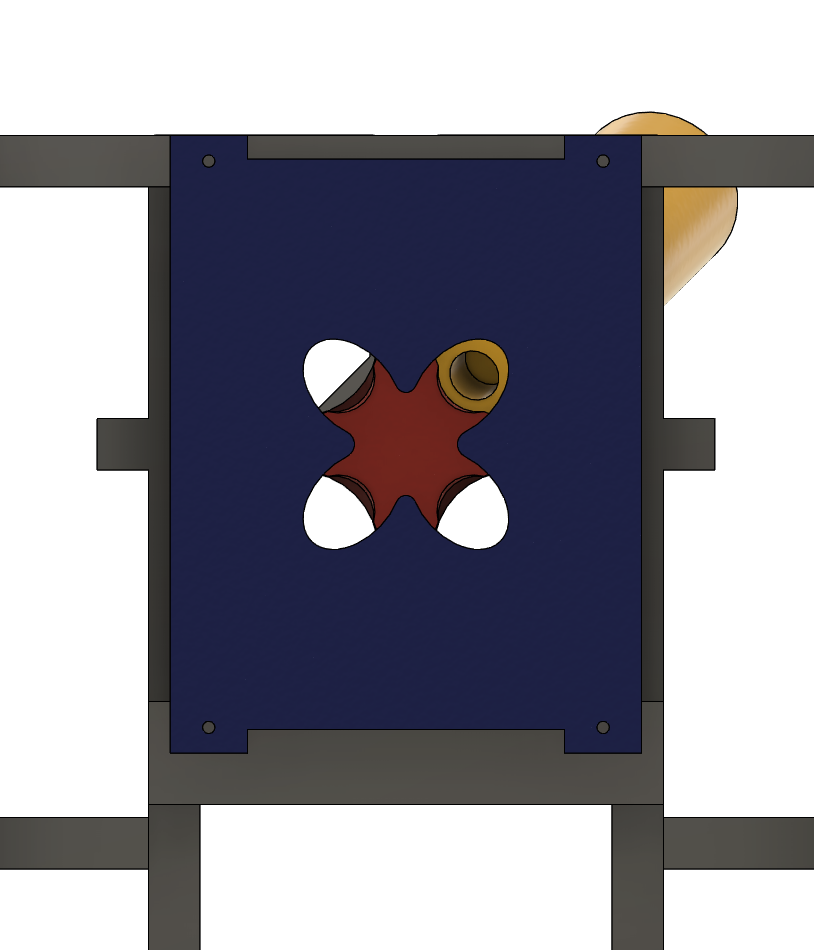
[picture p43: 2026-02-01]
rover/img/sprayer_assembly_bottom.png

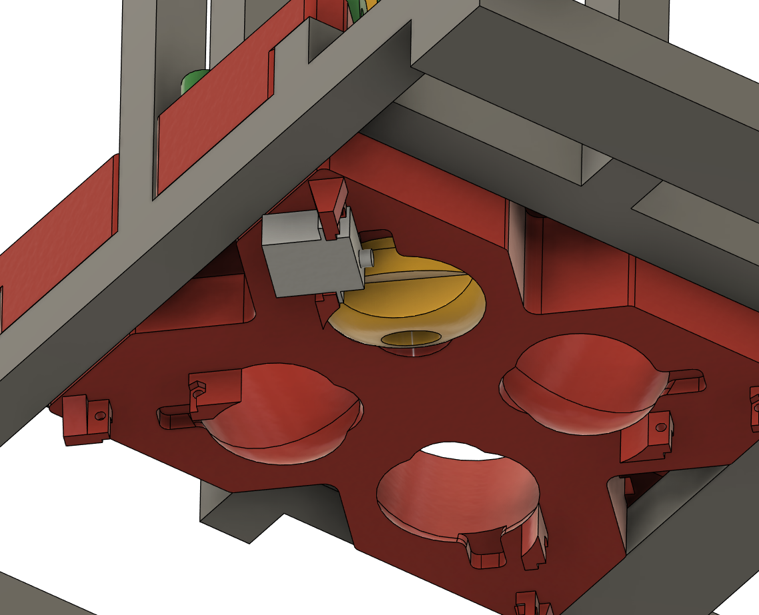
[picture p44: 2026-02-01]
rover/img/sprayer_assembly_bottom_nocover.png

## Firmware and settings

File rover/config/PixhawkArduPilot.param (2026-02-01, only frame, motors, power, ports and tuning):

ATC_SPEED_D,0
ATC_SPEED_D_FF,0
ATC_SPEED_FF,0
ATC_SPEED_FLTD,0
ATC_SPEED_FLTE,10
ATC_SPEED_FLTT,0
ATC_SPEED_I,0.2
ATC_SPEED_IMAX,1
ATC_SPEED_NEF,0
ATC_SPEED_NTF,0
ATC_SPEED_P,0.2
ATC_SPEED_PDMX,0
ATC_SPEED_SMAX,0
ATC_STR_ACC_MAX,0
ATC_STR_ANG_P,4
ATC_STR_RAT_D,0
ATC_STR_RAT_D_FF,0
ATC_STR_RAT_FF,0.2
ATC_STR_RAT_FLTD,0
ATC_STR_RAT_FLTE,10
ATC_STR_RAT_FLTT,0
ATC_STR_RAT_I,0.1
ATC_STR_RAT_IMAX,1
ATC_STR_RAT_MAX,120
ATC_STR_RAT_NEF,0
ATC_STR_RAT_NTF,0
ATC_STR_RAT_P,0.15
ATC_STR_RAT_PDMX,0
ATC_STR_RAT_SMAX,0
BATT_AMP_OFFSET,0
BATT_AMP_PERVLT,17
BATT_ARM_MAH,0
BATT_ARM_VOLT,0
BATT_CAPACITY,2200
BATT_CRT_MAH,0
BATT_CRT_VOLT,0
BATT_CURR_PIN,3
BATT_FS_CRT_ACT,0
BATT_FS_LOW_ACT,0
BATT_FS_VOLTSRC,0
BATT_LOW_MAH,0
BATT_LOW_TIMER,10
BATT_LOW_VOLT,0
BATT_MONITOR,4
BATT_OPTIONS,0
BATT_SERIAL_NUM,-1
BATT_VLT_OFFSET,0
BATT_VOLT_MULT,10.1
BATT_VOLT_PIN,2
BATT2_MONITOR,0
BATT3_MONITOR,0
BATT4_MONITOR,0
BATT5_MONITOR,0
BATT6_MONITOR,0
BATT7_MONITOR,0
BATT8_MONITOR,0
BATT9_MONITOR,0
FLTMODE_GCSBLOCK,0
FRAME_CLASS,1
FRAME_TYPE,0
INS_GYRO_FILTER,4
INS_HNTCH_ENABLE,0
MOT_PWM_FREQ,16
MOT_PWM_TYPE,5
MOT_SAFE_DISARM,0
MOT_SLEWRATE,0
MOT_SPD_SCA_BASE,1
MOT_STR_THR_MIX,0.5
MOT_THR_MAX,100
MOT_THR_MIN,0
MOT_THST_ASYM,1
MOT_THST_EXPO,0
MOT_VEC_ANGLEMAX,0
SERIAL0_BAUD,115
SERIAL0_PROTOCOL,2
SERIAL1_BAUD,460
SERIAL1_OPTIONS,0
SERIAL1_PROTOCOL,23
SERIAL2_BAUD,230
SERIAL2_OPTIONS,0
SERIAL2_PROTOCOL,2
SERIAL3_BAUD,230
SERIAL3_OPTIONS,0
SERIAL3_PROTOCOL,5
SERIAL4_BAUD,230
SERIAL4_OPTIONS,0
SERIAL4_PROTOCOL,-1
SERIAL5_BAUD,230
SERIAL5_OPTIONS,0
SERIAL5_PROTOCOL,-1
SERVO1_FUNCTION,62
SERVO1_MAX,1650
SERVO1_MIN,1000
SERVO1_REVERSED,0
SERVO1_TRIM,1650
SERVO2_FUNCTION,59
SERVO2_MAX,1650
SERVO2_MIN,1000
SERVO2_REVERSED,0
SERVO2_TRIM,1000
SERVO3_FUNCTION,59
SERVO3_MAX,1650
SERVO3_MIN,1000
SERVO3_REVERSED,0
SERVO3_TRIM,1000
SERVO4_FUNCTION,62
SERVO4_MAX,1650
SERVO4_MIN,1000
SERVO4_REVERSED,0
SERVO4_TRIM,1650
SERVO5_FUNCTION,57
SERVO5_MAX,1900
SERVO5_MIN,1000
SERVO5_REVERSED,0
SERVO5_TRIM,1500
SERVO6_FUNCTION,58
SERVO6_MAX,1900
SERVO6_MIN,1000
SERVO6_REVERSED,0
SERVO6_TRIM,1500
SERVO7_FUNCTION,60
SERVO7_MAX,2500
SERVO7_MIN,500
SERVO7_REVERSED,0
SERVO7_TRIM,1500
SERVO8_FUNCTION,61
SERVO8_MAX,2500
SERVO8_MIN,500
SERVO8_REVERSED,0
SERVO8_TRIM,1500
SERVO9_FUNCTION,74
SERVO9_MAX,2000
SERVO9_MIN,1000
SERVO9_REVERSED,0
SERVO9_TRIM,1500

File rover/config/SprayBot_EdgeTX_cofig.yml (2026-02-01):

semver: 2.11.4
header:
  name: SprayBot
  bitmap: ""
  labels: ""
  modelId:
    0:
      val: 0
noGlobalFunctions: 0
thrTrim: 0
trimInc: 0
displayTrims: 0
ignoreSensorIds: 0
showInstanceIds: 0
disableThrottleWarning: 0
enableCustomThrottleWarning: 0
customThrottleWarningPosition: 0
beepANACenter: 0
extendedLimits: 1
extendedTrims: 0
throttleReversed: 0
checklistInteractive: 0
flightModeData:
  0:
    trim:
      0:
        value: -10
        mode: 0
      1:
        value: -26
        mode: 0
      3:
        value: 20
        mode: 0
    name: ""
    fadeIn: 0
    fadeOut: 0
mixData:
  - destCh: 0
    srcRaw: I0
    weight: 100
    swtch: NONE
    curve:
      type: 0
      value: 0
    delayPrec: 0
    delayUp: 0
    delayDown: 0
    speedPrec: 0
    speedUp: 0
    speedDown: 0
    carryTrim: 0
    mltpx: ADD
    mixWarn: 0
    flightModes: 000000000
    offset: 0
    name: ""
  - destCh: 1
    srcRaw: I2
    weight: 100
    swtch: NONE
    curve:
      type: 0
      value: 0
    delayPrec: 0
    delayUp: 0
    delayDown: 0
    speedPrec: 0
    speedUp: 0
    speedDown: 0
    carryTrim: 0
    mltpx: ADD
    mixWarn: 0
    flightModes: 000000000
    offset: 0
    name: ""
  - destCh: 2
    srcRaw: I1
    weight: 100
    swtch: NONE
    curve:
      type: 0
      value: 0
    delayPrec: 0
    delayUp: 0
    delayDown: 0
    speedPrec: 0
    speedUp: 0
    speedDown: 0
    carryTrim: 0
    mltpx: ADD
    mixWarn: 0
    flightModes: 000000000
    offset: 0
    name: ""
  - destCh: 3
    srcRaw: I3
    weight: 100
    swtch: NONE
    curve:
      type: 0
      value: 0
    delayPrec: 0
    delayUp: 0
    delayDown: 0
    speedPrec: 0
    speedUp: 0
    speedDown: 0
    carryTrim: 0
    mltpx: ADD
    mixWarn: 0
    flightModes: 000000000
    offset: 0
    name: ""
  - destCh: 4
    srcRaw: SA
    weight: 100
    swtch: NONE
    curve:
      type: 0
      value: 0
    delayPrec: 0
    delayUp: 0
    delayDown: 0
    speedPrec: 0
    speedUp: 0
    speedDown: 0
    carryTrim: 0
    mltpx: ADD
    mixWarn: 0
    flightModes: 000000000
    offset: 0
    name: ""
  - destCh: 5
    srcRaw: SD
    weight: 100
    swtch: NONE
    curve:
      type: 0
      value: 0
    delayPrec: 0
    delayUp: 0
    delayDown: 0
    speedPrec: 0
    speedUp: 0
    speedDown: 0
    carryTrim: 0
    mltpx: ADD
    mixWarn: 0
    flightModes: 000000000
    offset: 0
    name: ""
  - destCh: 6
    srcRaw: SB
    weight: 100
    swtch: NONE
    curve:
      type: 0
      value: 0
    delayPrec: 0
    delayUp: 0
    delayDown: 0
    speedPrec: 0
    speedUp: 0
    speedDown: 0
    carryTrim: 0
    mltpx: ADD
    mixWarn: 0
    flightModes: 000000000
    offset: 0
    name: ""
  - destCh: 7
    srcRaw: SC
    weight: 100
    swtch: NONE
    curve:
      type: 0
      value: 0
    delayPrec: 0
    delayUp: 0
    delayDown: 0
    speedPrec: 0
    speedUp: 0
    speedDown: 0
    carryTrim: 0
    mltpx: ADD
    mixWarn: 0
    flightModes: 000000000
    offset: 0
    name: ""
  - destCh: 8
    srcRaw: SE
    weight: 100
    swtch: NONE
    curve:
      type: 3
      value: 1
    delayPrec: 0
    delayUp: 0
    delayDown: 0
    speedPrec: 0
    speedUp: 0
    speedDown: 0
    carryTrim: 0
    mltpx: ADD
    mixWarn: 0
    flightModes: 000000000
    offset: 0
    name: ""
  - destCh: 11
    srcRaw: SE
    weight: 100
    swtch: NONE
    curve:
      type: 3
      value: 2
    delayPrec: 0
    delayUp: 0
    delayDown: 0
    speedPrec: 0
    speedUp: 0
    speedDown: 0
    carryTrim: 0
    mltpx: ADD
    mixWarn: 0
    flightModes: 000000000
    offset: 0
    name: ""
limitData:
  0:
    min: 0
    max: 0
    revert: 0
    offset: 0
    ppmCenter: 0
    symetrical: 0
    name: ""
    curve: 32
  1:
    min: 0
    max: 0
    revert: 0
    offset: 0
    ppmCenter: 0
    symetrical: 0
    name: ""
    curve: 32
  3:
    min: 0
    max: 0
    revert: 0
    offset: 0
    ppmCenter: 0
    symetrical: 0
    name: ""
    curve: 32
expoData:
  - srcRaw: Rud
    scale: 0
    mode: 3
    chn: 0
    swtch: NONE
    flightModes: 000000000
    weight: 100
    offset: 0
    curve:
      type: 1
      value: 0
    trimSource: 0
    name: ""
  - srcRaw: Ele
    scale: 0
    mode: 3
    chn: 1
    swtch: NONE
    flightModes: 000000000
    weight: 100
    offset: 0
    curve:
      type: 1
      value: 0
    trimSource: 0
    name: ""
  - srcRaw: Thr
    scale: 0
    mode: 3
    chn: 2
    swtch: NONE
    flightModes: 000000000
    weight: 100
    offset: 0
    curve:
      type: 1
      value: 0
    trimSource: 0
    name: ""
  - srcRaw: Ail
    scale: 0
    mode: 3
    chn: 3
    swtch: NONE
    flightModes: 000000000
    weight: 100
    offset: 0
    curve:
      type: 1
      value: 0
    trimSource: 0
    name: ""
inputNames:
  0:
    val: Rud
  1:
    val: Ele
  2:
    val: Thr
  3:
    val: Ail
curves:
  0:
    type: 1
    smooth: 0
    points: -3
    name: ""
  1:
    type: 0
    smooth: 0
    points: -3
    name: ""
  31:
    type: 1
    smooth: 0
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
